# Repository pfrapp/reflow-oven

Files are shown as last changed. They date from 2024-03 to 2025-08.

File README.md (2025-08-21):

# reflow-oven
DIY reflow oven for SMD soldering

## Scope

In this project, we build an oven for reflow soldering of SMD (surface mount device)
parts, such as for instance microcontrollers etc.
In general, it will help to move away from THT (through hole technology)
boards and enter the realm of SMT (surface mount technology) boards.
This saves space, helps to get rid of evaluation-board-style setups,
and enables fully embedded circuits.
It basically makes the PCBs more professional and less tinker-ish.

This project is inspired by a reflow oven that I had at the university.
It was a predecessor of this one that you can currently buy at Beta Layout.
https://eu.beta-layout.com/estore/order_product_details.html?wg=1&p=740

Another inspiration is this instructable
https://www.instructables.com/DIY-REFLOW-OVEN/
that shows how to build a DIY oven.

The latter resource ends up with a self-contained oven, as the author wants
to be able to use it as a stand-alone tool.
It looks really professional and solid.

In this project, I just want to get the oven working in a first step.
Furthermore, I want to use the oven to build an improved version of the controller board
(kind of in a bootstrapping manner).
Also, the oven shall be usable and controllable from my computer.
For this reason, I will not disassemble the oven itself nor use an LCD
display, but just create an MVP which is a controller that
uses the actual oven as is.

## Idea

The general idea is to use an off-the-shelf pizza oven as the central
heating element or oven.
In the process of reflow soldering, we need to ensure that the temperature
follows a *reflow soldering profile*.

Therefore, we use a temperature probe to measure the temperature and
feed it back to a controller which generates the control signal.

This is a PWM signal,
as the temperature dynamics is very slow and hence acts as a natural
low-pass filter.
As the controller can only provide the signal, but not the actual power,
we use a solid-state relay (SSR) as the actuator
in order to transform the uC signal
to a mains voltage signal.

The controller algorithm runs on a Raspberry Pi. It is connected via
USB to a Cortex M4 microcontroller. The latter is used
to acquire the temperature signal and to create the PWM signal.

## Components

Here is an overview of the essential required components.

| Component | Manufacturer | Description | Distributor | Order no. | Price (Euro)  |
|---|---|---|---|---|---|
| SSR | Finder | Steck-/Printrelais, 1x UM, 250V/10A, 5V, RM3,2 | Reichelt | FIN 43.41.7 5V  | 5.95 |
| Temperatur probe | UNI-T | Temperaturfuehler, Typ K, universal | Reichelt | UT TF-K | 3.95 |
| Cortex M4 Eval Board | TI | TM4C1236 Evaluation Board with breakout pins | DigiKey | 2314937 | ca. 18 |
| Pizza oven | Severin | TO 2045 Oven, 1500 W, 100 to 230 deg C | Amazon | | 60 |
| Fuse | | Feinsicherung 5x20mm, superflink (ff), 8A | Reichelt | ESKA 520.126 | ca. 2 |
| Fuse holder | | 5 x 20 mm, 250 V, 10 A, black | Reichelt | SCH 31010045 | 1.50 |
| Temperature converter | Maxim Integrated  | MAX6675 (incl. cold junction compensation) | Voelkner | R025452 | ca. 7 |

### SSR

If there is no voltage applied at the input, then pins 11 and 12
(12 being the one close to A1 and A2) are connected.
Pins 11 and 14 are not connected.

The measured resistance between A1 and A2 is 97 Ohm for the 5V DC relay.

Hypothesis: If voltage is applied between A1 and A2 (use additional 22 Ohm resistor, transistor and impedance converter),
then pins 11 and 14 are connected.

This hypothesis is confirmed (using the lab supply):
Attaching 5 V via a 22 Ohm resistor to A1, and putting A2 on ground, makes pins 11 and 14 connected (no
resistance, connectivity test is positive).
Pins 11 and 12 are then disconnected.

### Temperature probe

When the type K thermocouple is plugged into a volt meter,
one can see 0.0 mV.
This is because both the tip as well as the cold junction
are at the same temperature.

If the tip is heated by breathing at it, the voltage rises from 0.1 mV up to 0.3 mV.
When the tip is being put into an open oven that had a nominal temperature of 225 deg C,
the voltage rises to 2.0 mV or 2.1 mV.

Looking at the table from the second reference, this means that the temperature delta
is around 50 deg C (that is, ca. 70 deg C), which seems plausible given that the oven is open
and one can easily put the hand into it.

Resources
1. https://blog.beamex.com/de/thermoelement-kaltstellenkompensation-vergleichsstelle
2. https://www.omega.de/temperature/Z/pdf/z204-205iec.pdf

### Microcontroller

We use a Cortex M4 on a Tiva evaluation board.
It can be connected to the Raspberry Pi via USB.
The Raspberry Pi is connected to the host PC via Wi-Fi.

This allows
for the complete galvanic isolation between host PC
and reflow oven controller.

## Controller PCB

The controller board is a two-stage amplifier.
The signal from the microcontroller is first amplified using a BJT.
This signal is then used to control a relay.

Yet another stage is present on the Tiva board: It turned out that the
uC pins cannot reliably drive the BJT, so I introduced an impedance converter
using an OpAmp, see the following subsection.

### Impedance converter

Due to the switching of the relay, there are some voltage spikes on the transistor,
that is, on the low voltage side of the relay.

Those spikes are less pronounced when using the lab supply and more
pronounced when using the AD/DC converter.
They are there in any case though.

For this reason, an impedance converter or buffer is needed between the
uC pin and the controller board.

So far I tested the setup using this impedance converter and a lab supply
and it works.
In oder to test it without the lab supply I need a second AC/DC converter,
as the OpAmp needs a dual rail supply.

## Controller software

### Modelling of the reflow oven dynamics

The plant is modelled by a time delay followed by two first-order lag elements.

The parameters of the plant are identified by applying a step function
onto the oven. A 30% and 50% PWM signal is used for the step height.
Also, a 100% PWM step is applyied until a temperature of 100 deg C is reached.
In that case, also the cooling down is measured.

Here are some more details for the motivation of a first-order lag.
Note that we assume that there are two in order to model the
different behavior when heating and when cooling.
```
d_theta/dt = q_zu - q_ab

q_zu = K*u
q_ab = alpha*theta

K ... Proportional zur Leistung des Ofens
theta ... Abkuehlkoeffizient

d_theta/dt = K*u - alpha*theta

d_theta/dt + alpha*theta = K*u

s*Theta + alpha*Theta = K*U

(s + alpha) * Theta = K * U

G = Theta / U = K/(s + alpha)

```

Later a more complex model is used. You can find it in the Jupyter notebook.

### Control design

A PID controller is used for temperature control.
The parameters of a PI controller have been parameterized by the Ziegler-Nichols method.
Based on that, a PID controller has been manually tuned using the experimentally
identified plant.

## Tiva pin usage and connection

| Pin on Tiva | Connected with | Description |
|---|---:|---:|
| GND | Analog Thermo amplifier GND | Ground |
| PE3 | Analog Thermo amplifier between 6.8k and 18k | ADC input |
| GND | GND of BMP280 evaluation board | Ground |
| +3.3V | VCC of BMP280 evaluation board | Supply voltage |
| PA6 | SCL of BMP280 evaluation board | I2C clock |
| PA7 | SDA of BMP280 evaluation board | I2C data |
| PB6 | Digital Thermo amplifier MISO | SPI data |
| PB5 | Digital Thermo amplifier CS | SPI CS |
| PB4 | Digital Thermo amplifier Clock | SPI clock |
| PF4 | Controller board pin 2 | Relay control |

See also the following block diagram overview.

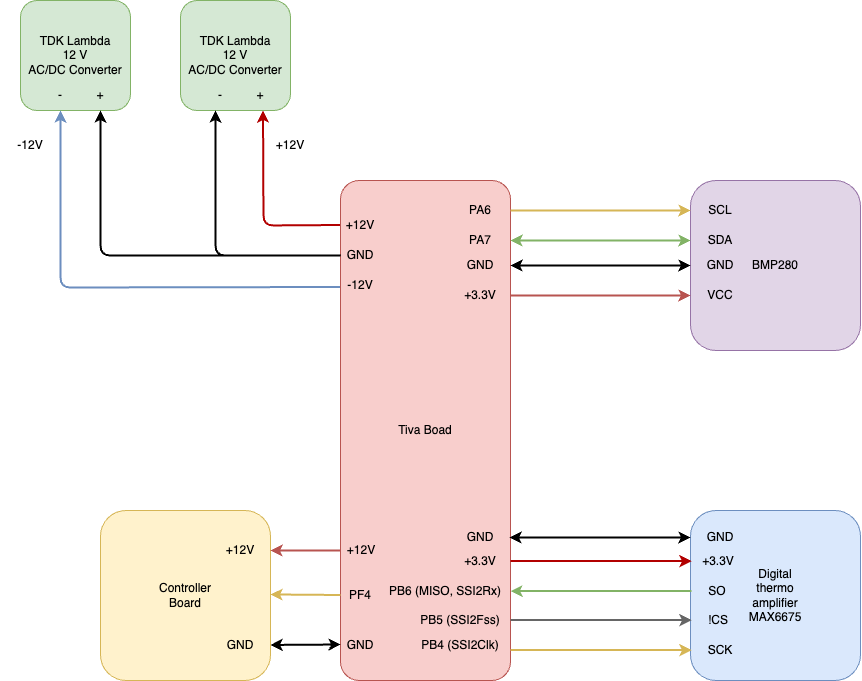
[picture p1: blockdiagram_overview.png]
Block diagram overview


## General todos

- Add note to add LED signaling open thermocouple
- Add note to add LED signaling request to open door (manually)
- Add manual with important points, for instance
  - check for polarity of diodes and LEDs
  - Alignment of ICs

## Reference solder profiles

- https://www.7pcb.com/blog/lead-free-reflow-profile
- Data sheet of my solder paste
  https://de.beta-layout.com/elektronik-shop/loetzinn-lotpaste/10753-smd-lotpaste-iso-cream/
- TI application report
  **SPRABY1A MSL Ratings and Reflow Profiles** \
  https://www.ti.com/lit/an/spraby1a/spraby1a.pdf?ts=1741440364541

## Solder reports

### First SMD soldering with this setup (Oct-30, 2024)

- Lead-free HASL PCB (that is, no ENIG)
- No uC soldered (otherwise ENIG required)
- Stencil is required
- Soldered components: 0805 C, 0805 R (contain labels), Diodes, LEDs, OpAmps and other ICs
- Some parts on the PCB did not solder well --> longer preheat time, higher peak temperature, longer reflow time
- Fragmented setup was quite a mess --> higher integration of controller boards, fixture of the BMP280
- Power via lab supply --> Use TDK Lambdas in the future
- Timing of door opening to be made easier
- Application of solder paste --> not too much, also remove where there is too much before placing the part
- Add note to check for polarity of diodes and LEDs
- Reworking requires (no clean) flux

Time above 217 deg C: 52.5 seconds (with opening the door)<br />
Time between 150 and 180 deg C: 77.0 seconds<br />
Peak temperature: 237.0 deg C

### Second SMD soldering (Dec-23, 2024)

#### Compared with the first SMD soldering, I changed the following things:
- Adjusted solder temperature profile with the goal to allow for
  - more preheat time (goal reached)
  - higher peak temperature (not reached, peak temperature was actually slightly lower)
  - longer reflow time (goal reached)
- Better solder paste application
  - I made sure to apply the solder paste in a single round. That means,
    I ensured that I had enough of the paste on the upper edge
    of the stencil.
  - Then I went down slowly *once* while pressing firmly onto the stencil.
    It is important to not go back and forth (potentially allowing for too much solder paste).
  - The described procedure favors less solder paste being applied.
    As a consequence, I did not have to remove any surplus solder paste.
- I did *not* use a separate PCB to attach the thermocouple.
  Rather than that, I braided the thermocouple wire trough the grating of the grillage.
  I made sure that the tip was directly in between two grates, thus avoiding any contact
  of the termocouple tip with the metal grates (or with a dedicated PCB).
- I made the hint to open the door more prominent so that it could be
  seen when standing at the oven and looking on to the computer screen.
- I did solder a microcontroller. It was the 64-pin TM4C123GH6PM.
  Note that I ordered lead-free HASL (that is, the ENIG finish was not necessary).

#### Observations and facts
  - When opening the door, the thermocouple was detected as open, hence
    resulting in non-usable temperature measurements.
    As this was the cool-down phase anyway, no harm was induced.
  - I slipped while placing the Cortex onto the PCB.
    Apparently that was not a show-stopper.
    As can be seen on the magnified pictures I took, the solder paste
    had not been smeared away from the Cortex, but rather only between the pins.
  - The overall solder result was surprisingly good. I did not have to do any
    reworking and hence also did not need to use the no-clean flux.
  - It was raining, but I wanted to finish before Christmas, so I used an umbrella
    to protect the oven.

#### Open todos and fixes after this second soldering round
- USB Stencil checken (also ob Anmerkungen von jlcpcb umgesetzt wurden, erst in KiCad Lib, dann im Projekt)
- Highlight beim Bestuecken (z.B. eine PDF Seite pro Teil, erstellen via KiCad Python Script)
- Sanft positionieren (z.B. Halter fuer Pinzette konstruieren?)
- Dioden Polarity dokumentieren
- LEDs Polarity dokumentieren (fuer jede einzelne LED, da potentiell unterschiedlich pro Typ und zumindest unterschiedlich markiert)
  - Bei "Tetris" artigem Bild ist das kleine Quadrat die Kathode
  - Bei Dreieck ist die Spitze die Kathode
  - Auf der Vorderseite gibt es einen kleine gruene Markierung bei der Kathode
  - Auf dem Silk ist die geschlossene Seite die Kathode, die Anode ist offen
- LED Farben fixen im Schematic (2 mehr blue, 2 weniger gruen)
- Silk fuer Montage USB (also genaue Ausrichtung)
- Cortex Stencil checken (unterschiedlich grosse Luecken auf den Seiten)
  --> hat letztlich nichts gemacht
- SMD Bauteile einsortieren
- Inventur und nachbestellen, auch Resistors, Caps.
- Art Kreuze am Stencil fuer Ausrichtung (in allen 4 Ecken)
- Thermocouple open/closed sollte beides ueber LED direkt sichtbar sein
- Reflow Oven braucht einen Baking Modus (verschiedene Dauern und Temperaturen sollten auswaehlbar sein)
- Spannungsversorgung +12V/-12V auf einen Stecker packen, damit keine unipolare Spannungsversorgung moeglich ist (die mir schon mal den uC kaputt gemacht hat)
- Widerstand oder Zener auf PF4 Signal legen
```
(GPIO Output) --- [ 4.7 kΩ Resistor ] ---+--- (OpAmp Non-Inverting Input)
                                          |
                                    [ 3.3 V Zener Diode ]
                                          |
                                         GND
```

#### Output of the Jupyter script for solder profile analysis

Time above 217 deg C: 114.99984027777778 seconds (with opening the door)<br />
Time between 150 and 180 deg C: 91.99987222222222 seconds<br />
Peak temperature: 1023.75 deg C

Note that there was an error due to the thermocouple being open.
The values are rather<br />

Time above 217 deg C: 60 seconds (with opening the door)<br />
Time between 150 and 180 deg C: 91.99987222222222 seconds<br />
Peak temperature: 233 deg C

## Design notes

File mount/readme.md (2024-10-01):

This folder contains the 3D models for the PCB and stencil mount.
Those are used to fixate the PCB and strencil while applying the soldering paste.

The idea is to be able to fixate the PCB and the stencil independently via screws.
No tape shall be used.

PCB without stencil
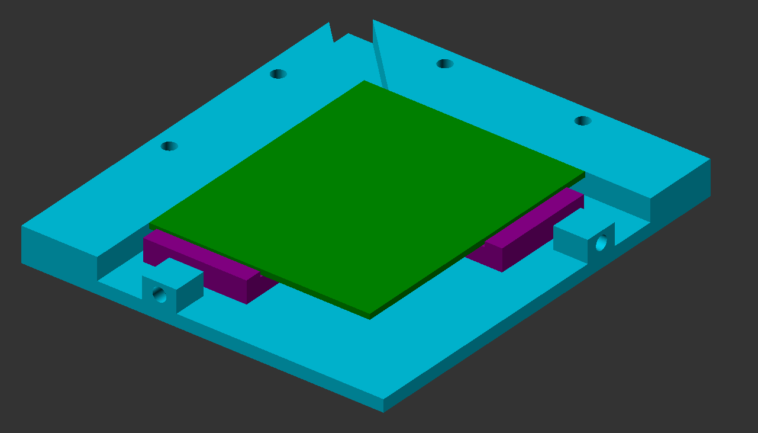
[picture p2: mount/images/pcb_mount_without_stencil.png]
PCB mount without stencil


PCB with stencil
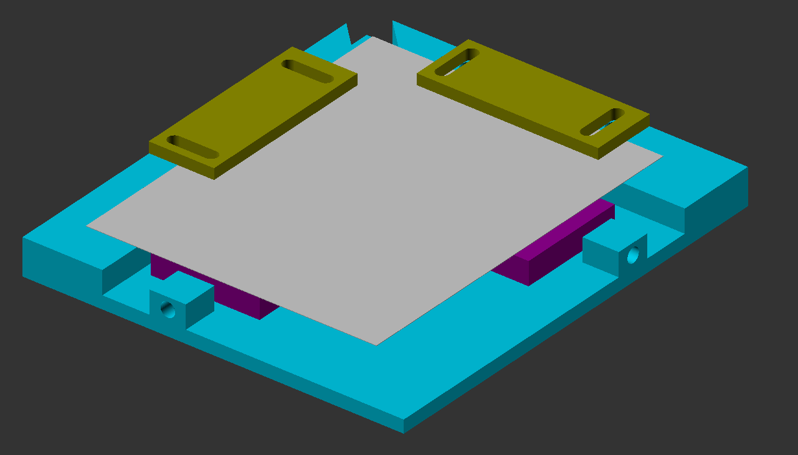
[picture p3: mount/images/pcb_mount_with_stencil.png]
PCB mount with stencil


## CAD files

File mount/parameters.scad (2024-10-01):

// Screw threads.
// Note that the depth is increased by 0.1 mm as compared
// to the data sheet.
// The diameter corresponds to the d3 from the data sheet,
// and the depth correponds to the L.

// M2
g_M2_thread_diameter = 3.2;
g_M2_thread_depth    = 4.1;

// M3
g_M3_thread_diameter = 4.0;
g_M3_thread_depth    = 5.8;

// Through holes.
// See for instance https://de.wikipedia.org/wiki/Durchgangsbohrung
g_M2_through_hole_diameter = 2.4;
g_M3_through_hole_diameter = 3.4;
g_M3_through_hole_diameter_large = 3.6;

// Offset between holes in stencil mount
stencil_mount_hole_offset = 40.0;

// Outer dimension of the PCB mount part
height_mount = 10.0;
length_mount = 105.0;
width_mount = 120.0;

// Thickness of the wall where the PCB is pushed against.
// This is used for the margins of the stencil which
// is larger than the PCB.
wall_thickness_mount = 14.0;

// Space for the stencil (at the top and left).
// Actually this is space for the stencil mount.
stencil_space = 8.0;

// Height of the PCB
height_pcb = 1.6;

// Height of the stencil
height_stencil = 0.15;

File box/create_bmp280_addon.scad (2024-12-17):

// Mount for the BMP280 temperature sensor (evaluation board).
// Should at some point be unified with the other boxes.
//
// BMP280 evaluation board
// - outer distances of holes: 13.30 mm
// - inner distances of holes: 7.20 mm
//
// --> Double hole diameter = 13.30 - 7.20 = 3.05 mm
// 2x M2 mit Unterlegscheibe (statt M3) wg. Positionstoleranz
//
// Distance between hole centeres: 0.5 * (13.30 + 7.20) = 10.25 mm
// (likely nominally 4 * 2.54 mm = 10.16 mm)
//
// Breite Auflageflaeche: 15 mm (mit Bohrungen mittig)
// Hoehe Auflageflaeche: 25 mm (Bohrungen jeweils am Rand)
//
// Hoehe des Bauteils: 20 mm


g_fn = 90;

g_spacing = 10.16;
g_holes_y = [-g_spacing / 2.0, g_spacing / 2.0];

// M2
g_M2_thread_diameter = 3.2;
g_M2_thread_depth    = 4.1;
g_M2_through_hole_diameter = 2.4;

width = 11;
height = 25;

roundness = 2;

module entity() {
    difference() {
        union() {   
            // Cube
            translate([-(width-roundness)/2,-(height-roundness)/2,10]) {
                minkowski() {
                sphere(r = 1, $fn = g_fn);
                linear_extrude(20-roundness, center=true)
                    square([width-roundness, height-roundness]);
                }
            }
            linear_extrude(3, center=false)
                scale([1.0, 2.0, 1.0])
                    circle(r = 12, $fn = g_fn);
        }
        union() {
            // Through holes
            for (y = g_holes_y) {
                translate([0.0, y, 0.0])
                    cylinder(h = 20, d = g_M2_through_hole_diameter, $fn = g_fn);
            }
            // Holes for thread mount
            for (y = g_holes_y) {
                translate([0.0, y, 20.0 - g_M2_thread_depth])
                    cylinder(h = g_M2_thread_depth, d = g_M2_thread_diameter, $fn = g_fn);
            }
        }
    }
}



entity();

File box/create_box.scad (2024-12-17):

// Box for the reflow controller
//
// Aktor/Ansteuerung Board Dimension: 90 x 60
// Bohrmuster: 82 x 52
// Rand: 10 links (hin zum uC), 20 rechts (hin zum Ofen und Netzspannung)

// Sensor/Digital Thermocouple Board Dimesion: 70 x 50
// Bohrmuster: 62 x 42
// Hinweis: Die Bohrung oben rechts ist um ca. 0.3 mm in y-Richtung verschoben.


// Notwendige Aenderungen:
// - Noch mehr Platz beim Stromanschluss vorsehen
// - Bohrungen fuer das Tiva Board mit Impedance Converter einfuegen
// - Deckel an der Seite abschliessen


g_fn = 90;

// Nominell 8 mm (gemessen), plus 0.2 mm Toleranz wg. 3D Drucker
d_stromkabel = 8.0 + 0.2;

g_bohrmuster_relay_board_x = [-41, 41];
g_bohrmuster_relay_board_y = [-26, 26];

g_bohrmuster_thermo_board_x = [-31, 31];
g_bohrmuster_thermo_board_y = [-21, 21];

module box() {
    translate([-60,-40,0])
        difference() {
            union() {
                cube([140,80,32]);
                translate([136,80,0])
                    cube([4,58,32]);
            }
            translate([0,2,1.5])
                cube([136,76,32.5]);
            translate([0,80,2])
                cube([136,115,32]);
            translate([0,0,2])
                cube([60,160,32]);
            translate([0,150,2])
                cube([140,45,35]);
            translate([42,100,0])
                cube([35,80,2]);
        }
}

module halter(pattern_x, pattern_y) {
    for (x = pattern_x) {
        for (y = pattern_y) {
            translate([x,y,0]) {
                cylinder(d=10, h=10, $fn=g_fn);
            }
        }
    }
}

module halter_hutschiene(pattern_x, pattern_y) {
    for (x = pattern_x) {
        for (y = pattern_y) {
            translate([x,y,0]) {
                cylinder(d=12, h=16, $fn=g_fn);
            }
        }
    }
}

// M3
module halter_loecher(pattern_x, pattern_y) {
    for (x = pattern_x) {
        for (y = pattern_y) {
            translate([x,y,0]) {
                translate([0,0,4.2])
                    cylinder(d=4.0, h=5.8, $fn=g_fn);
                cylinder(d=3.4, h=10, $fn=g_fn);
            }
        }
    }
}

// M4
module halter_loecher_hutschiene(pattern_x, pattern_y) {
    for (x = pattern_x) {
        for (y = pattern_y) {
            translate([x,y,0]) {
                translate([0,0,7.8])
                    cylinder(d=5.6, h=8.2, $fn=g_fn);
                cylinder(d=4.6, h=16, $fn=g_fn);
            }
        }
    }
}

module kabelfuehrung() {
    for (y = [-3,15]) {
        translate([70,y,23])
            rotate([0,90,0]) {
                cylinder(d=d_stromkabel, h=20, $fn=g_fn);
            }
    }
}

module quarter_cylinder(r, h) {
    difference() {
        cylinder(h=h, r=r, $fn=g_fn);
        translate([-r,0,0])
            cube([2*r, 2*r, 4*h], center=true);
        translate([0,-r,0])
            cube([2*r, 2*r, 4*h], center=true);
    }
}

// Bohrungen fuer die Laborstecker.
// Durchmesser: 8 mm (daher 8.2 mm wg. Toleranz).
module bohrungen_laborstecker() {
    g_laenge = 90.0;
    g_wanddicke = 5;
    g_hoehe = 30;
    
    
    d_bohrung_laborstecker = 8.2;
    translate([0,g_wanddicke,g_hoehe/2])
        rotate([90,0,0])
            linear_extrude(g_wanddicke, center=false) {
                translate([g_laenge/4,0,0])
                    circle(d=d_bohrung_laborstecker, $fn=g_fn);
                translate([g_laenge/2,0,0])
                    circle(d=d_bohrung_laborstecker, $fn=g_fn);
            }
    // Beschriftung
    font_size = 4.5;
    text_depth = 2;
    translate([g_laenge/4+0*d_bohrung_laborstecker,0,3*g_hoehe/4])
        rotate([90,0,0])
            translate([0,0,-text_depth])
                linear_extrude(text_depth, center=false)
                    text("T(-)",
                        font = "Arial Black",
                        size = font_size,
                        valign = "bottom",
                        halign = "center");
    translate([g_laenge/2+0*d_bohrung_laborstecker,0,3*g_hoehe/4])
        rotate([90,0,0])
            translate([0,0,-text_depth])
                linear_extrude(text_depth, center=false)
                    text("T(+)",
                        font = "Arial Black",
                        size = font_size,
                        valign = "bottom",
                        halign = "center");
}

module verbindung_halter() {
    // Grundform
    grundform_points = [[-52, -38], [-52, 40], [-38, 60], [-38, 150],
                        [55, 150], [38, 110], [38, 60], [42, 40], [42, -38],
                        [30, -38], [30, 40], [25, 60], [25, 110], [35, 140],
                        [-25, 140], [-25, 55], [-40, 35], [-40, -38]
                       ];
    linear_extrude(3.0)
        minkowski() {
            polygon(grundform_points);
            circle(r=2, $fn = g_fn);
        }
}

module entity() {
    difference() {
        union() {
            box();
            translate([-5,0,0])
                halter(g_bohrmuster_relay_board_x, g_bohrmuster_relay_board_y);
            translate([0,80,0])
                halter(g_bohrmuster_thermo_board_x, g_bohrmuster_thermo_board_y);
            // Hutschiene
            translate([-30,145,0])
                halter_hutschiene([0, 75], [0]);
            translate([80,40,2])
                rotate([0,0,180])
                    quarter_cylinder(r=12, h=30);
            translate([80,-40,2])
                rotate([0,0,90])
                    quarter_cylinder(r=12, h=30);
            verbindung_halter();
        }
        translate([-5,0,0])
            halter_loecher(g_bohrmuster_relay_board_x, g_bohrmuster_relay_board_y);
        translate([0,80,0])
            halter_loecher(g_bohrmuster_thermo_board_x, g_bohrmuster_thermo_board_y);
        // Loecher zur Befestigung des Deckels
        translate([80,0,23])
            halter_loecher([-5], [-35, 35]);
        // Loecher zur Befestigung der Hutschiene
        translate([-30,145,0])
            halter_loecher_hutschiene([0, 75], [0]);
        kabelfuehrung();
        translate([80,40,0])
            rotate([0,0,90])
                bohrungen_laborstecker();
    }
}


entity();
// translate([-16,0,32])
//     lid();

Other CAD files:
box/create_lid.scad
box/create_tiva_box_addon.scad
box/lid_part.scad
mount/create_assembly.scad
mount/create_pcb.scad
mount/create_pcb_mount.scad
mount/create_plate.scad
mount/create_stencil.scad
mount/create_stencil_mount.scad

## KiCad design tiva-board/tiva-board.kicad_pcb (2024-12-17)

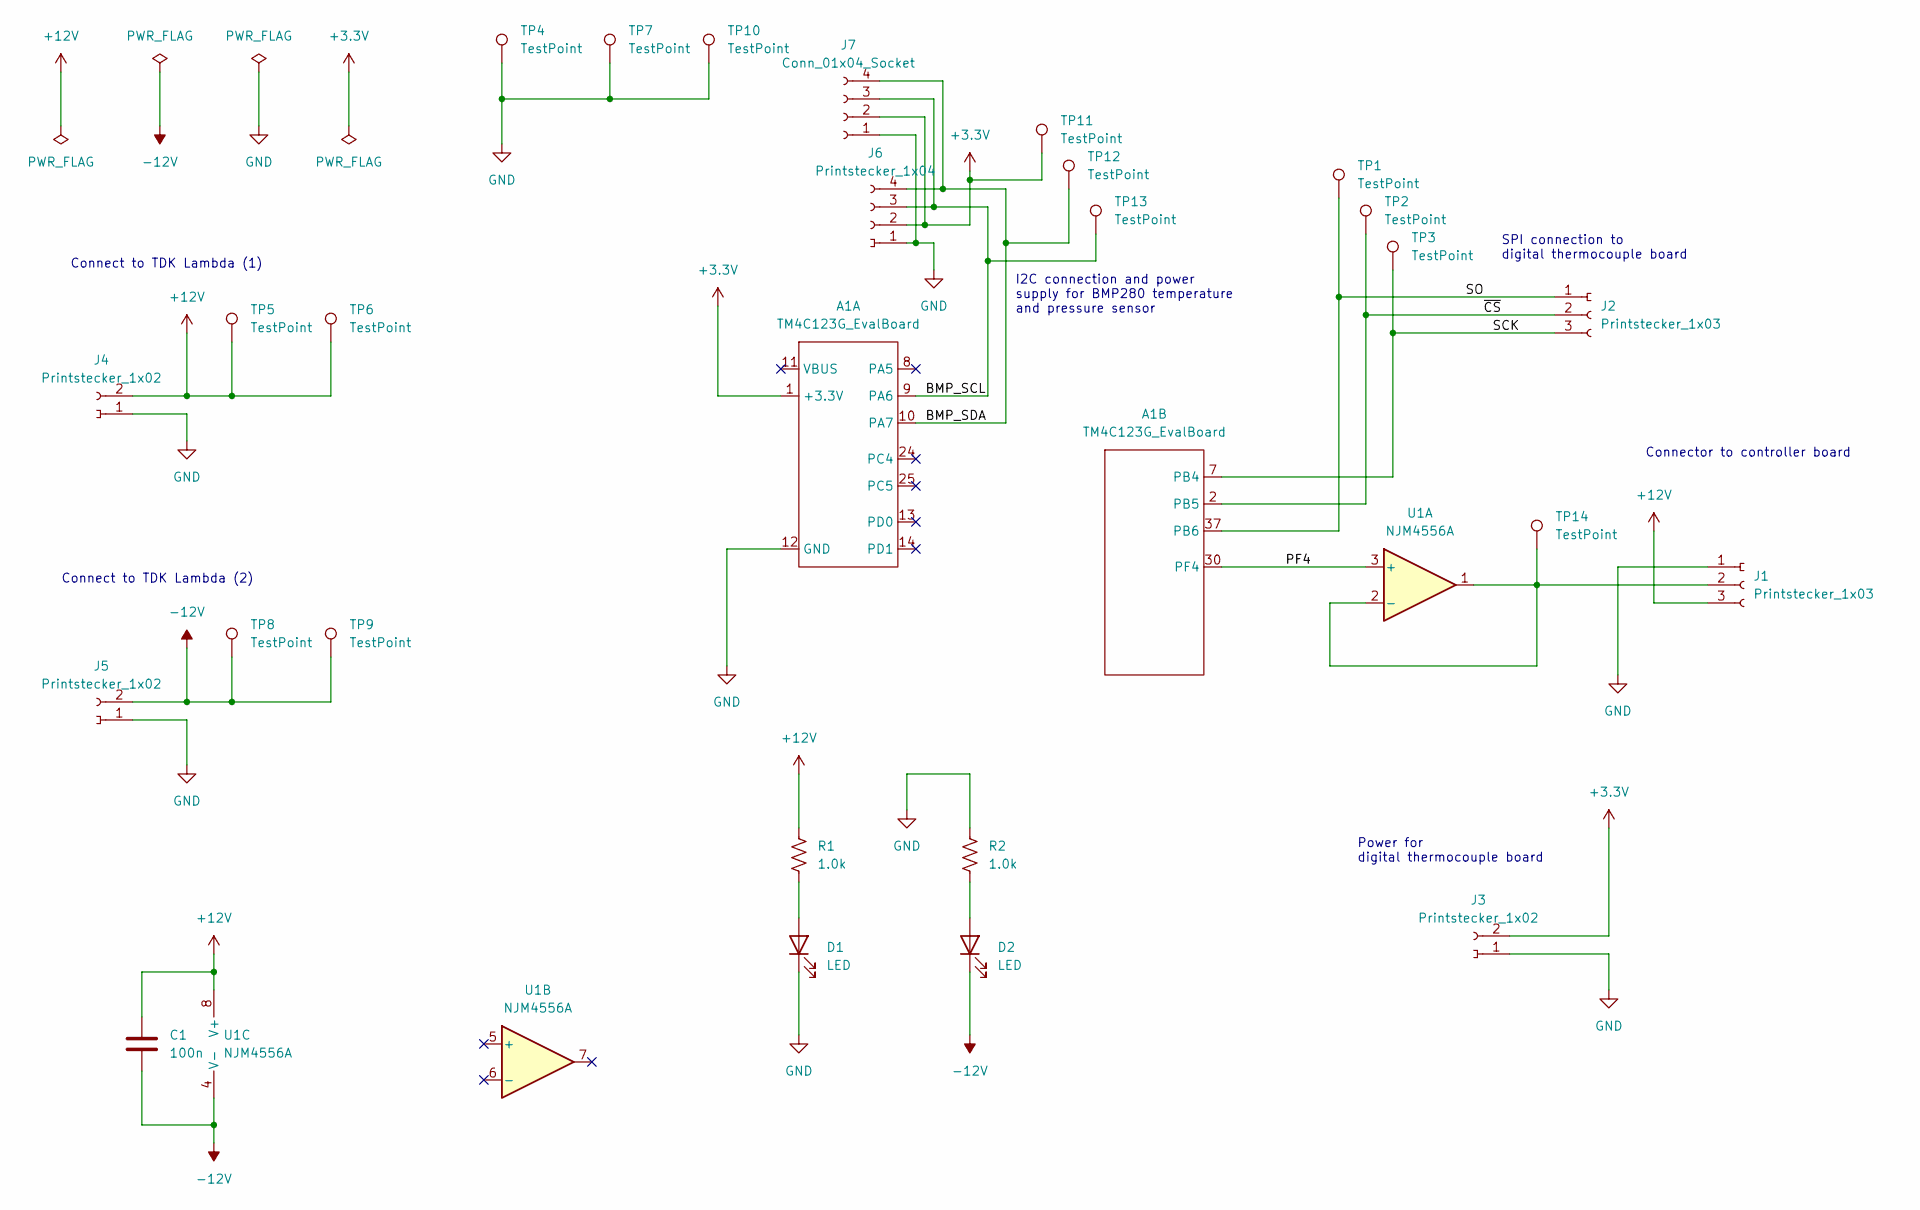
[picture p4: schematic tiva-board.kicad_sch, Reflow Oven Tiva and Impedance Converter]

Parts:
A1: TM4C123G_EvalBoard
C1: 100n; C_Disc_D5.0mm_W2.5mm_P2.50mm
D1, D2: LED; LED_D5.0mm
J1, J2: Printstecker_1x03; printstecker_1x03_P2.54mm
J3, J4, J5: Printstecker_1x02; printstecker_1x02_P2.54mm
J6: Printstecker_1x04; printstecker_1x04_P2.54mm
J7: Conn_01x04_Socket; PinSocket_1x04_P2.54mm_Vertical
R1, R2: 1.0k; R_Axial_DIN0207_L6.3mm_D2.5mm_P10.16mm_Horizontal
TP1, TP2, TP3, TP6, TP9, TP11, TP12, TP13, TP14: TestPoint; TestPoint_Pad_2.0x2.0mm
TP4, TP5, TP7, TP8, TP10: TestPoint; TestPoint_Plated_Hole_D2.0mm
U1: NJM4556A; DIP-8_W7.62mm

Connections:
+3.3V: A1.1 (+3.3V), J3.2, J6.2, J7.2, TP11.1
+12V: C1.1, J1.3, J4.2, R1.1, TP5.1, TP6.1, U1.8 (V+)
-12V: C1.2, D2.1 (K), J5.2, TP8.1, TP9.1, U1.4 (V-)
/BMP_SCL: A1.9 (PA6), J6.3, J7.3, TP13.1
/BMP_SDA: A1.10 (PA7), J6.4 (Pin_3), J7.4, TP12.1
/PF4: A1.30 (PF4), U1.3 (+)
/SCK: A1.7 (PB4), J2.3, TP3.1
/SO: A1.37 (PB6), J2.1, TP1.1
/~CS: A1.2 (PB5), J2.2, TP2.1
GND: A1.12 (GND), A1.31 (GND), D1.1 (K), J1.1, J3.1, J4.1, J5.1, J6.1, J7.1, R2.1, TP4.1, TP7.1, TP10.1
unnamed: D1.2 (A), R1.2
unnamed: D2.2 (A), R2.2
unnamed: J1.2, TP14.1, U1.1, U1.2 (-)

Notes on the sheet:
Power for digital thermocouple board
I2C connection and power supply for BMP280 temperature and pressure sensor
Connect to TDK Lambda (2)
Connect to TDK Lambda (1)
Connector to controller board
SPI connection to digital thermocouple board

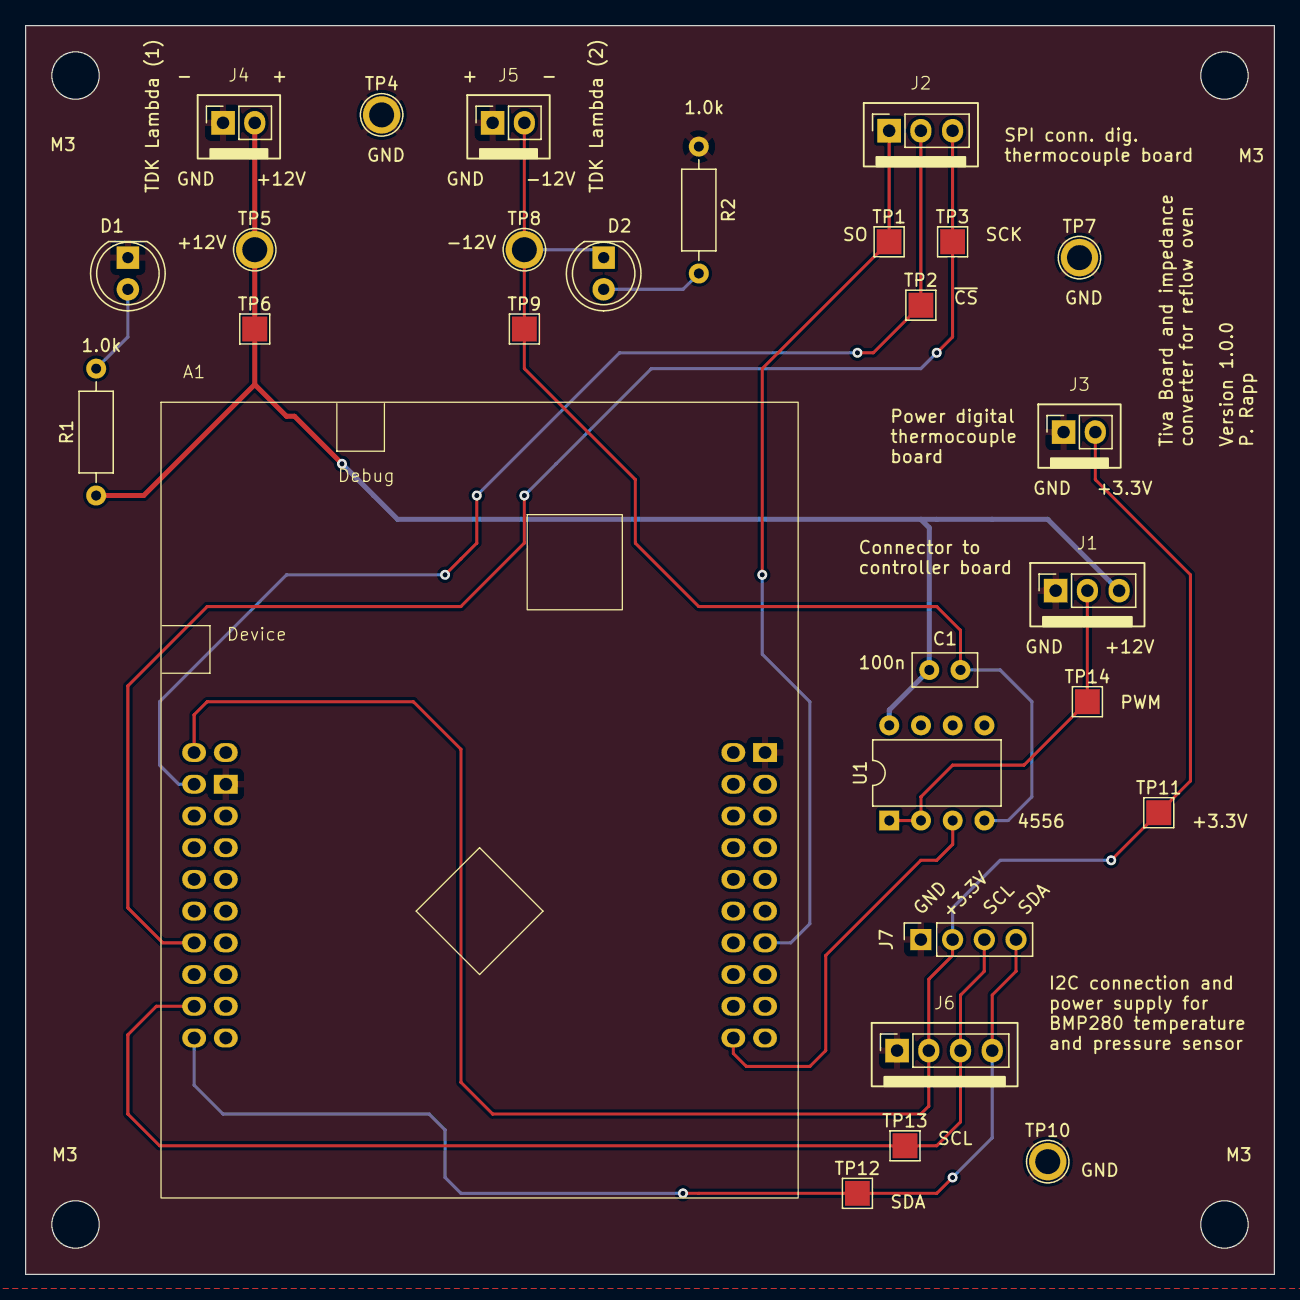
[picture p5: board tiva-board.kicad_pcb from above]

Board: 2 copper layers, 100.0 x 100.0 mm, 28 parts (0 on the bottom side), 13 nets.

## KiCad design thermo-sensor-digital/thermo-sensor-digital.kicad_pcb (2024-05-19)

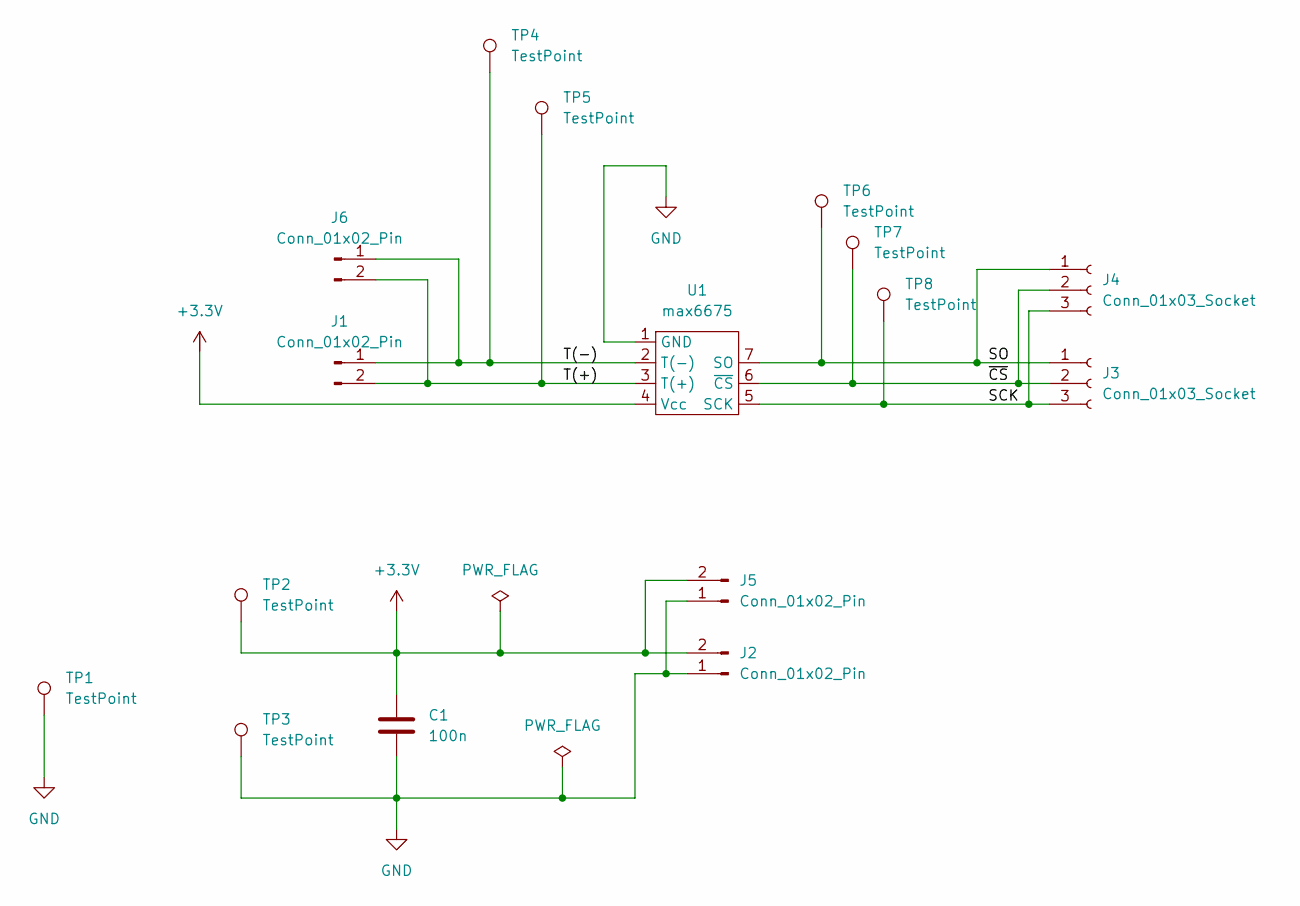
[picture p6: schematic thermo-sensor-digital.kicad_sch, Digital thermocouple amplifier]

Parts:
C1: 100n; C_Disc_D5.0mm_W2.5mm_P2.50mm
J1, J2, J5, J6: Conn_01x02_Pin; PinSocket_1x02_P2.54mm_Vertical
J3, J4: Conn_01x03_Socket; PinSocket_1x03_P2.54mm_Vertical
TP1: TestPoint; TestPoint_THTPad_4.0x4.0mm_Drill2.0mm
TP2, TP4, TP5, TP6, TP7, TP8: TestPoint; TestPoint_Pad_2.0x2.0mm
TP3: TestPoint; TestPoint_Plated_Hole_D2.0mm
U1: max6675

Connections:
+3.3V: C1.1, J2.2, J5.2, TP2.1, U1.4 (Vcc)
/SCK: J3.3, J4.3, TP8.1, U1.5 (SCK)
/SO: J3.1, J4.1, TP6.1, U1.7 (SO)
/T(+): J1.2, J6.2, TP5.1, U1.3 (T(+))
/T(-): J1.1, J6.1, TP4.1, U1.2 (T(-))
/~CS: J3.2, J4.2, TP7.1, U1.6 (~CS)
GND: C1.2, J2.1, J5.1, TP1.1, TP3.1, U1.1 (GND)

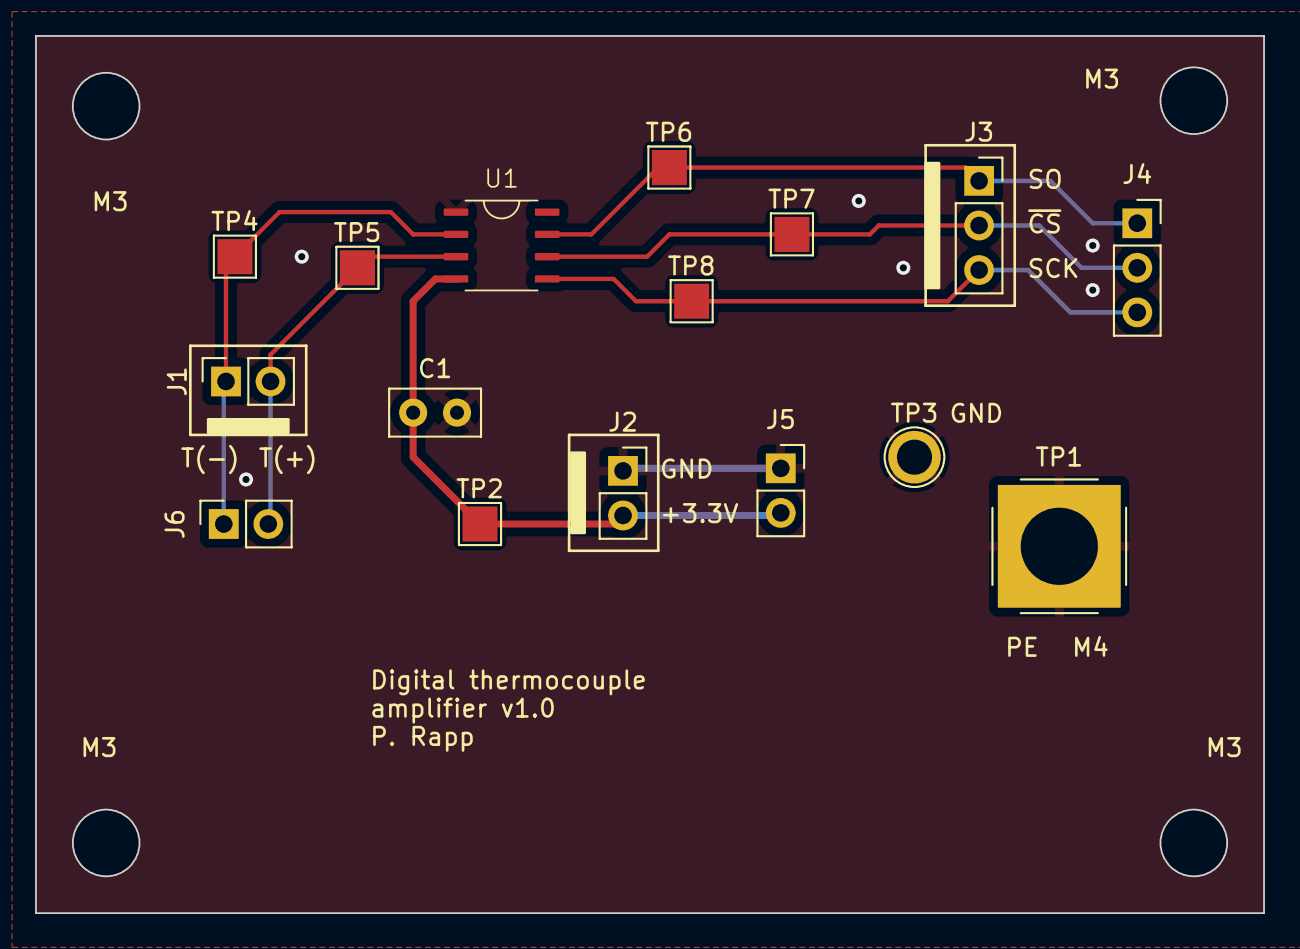
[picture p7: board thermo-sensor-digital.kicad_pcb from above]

Board: 2 copper layers, 70.0 x 50.0 mm, 16 parts (0 on the bottom side), 7 nets.

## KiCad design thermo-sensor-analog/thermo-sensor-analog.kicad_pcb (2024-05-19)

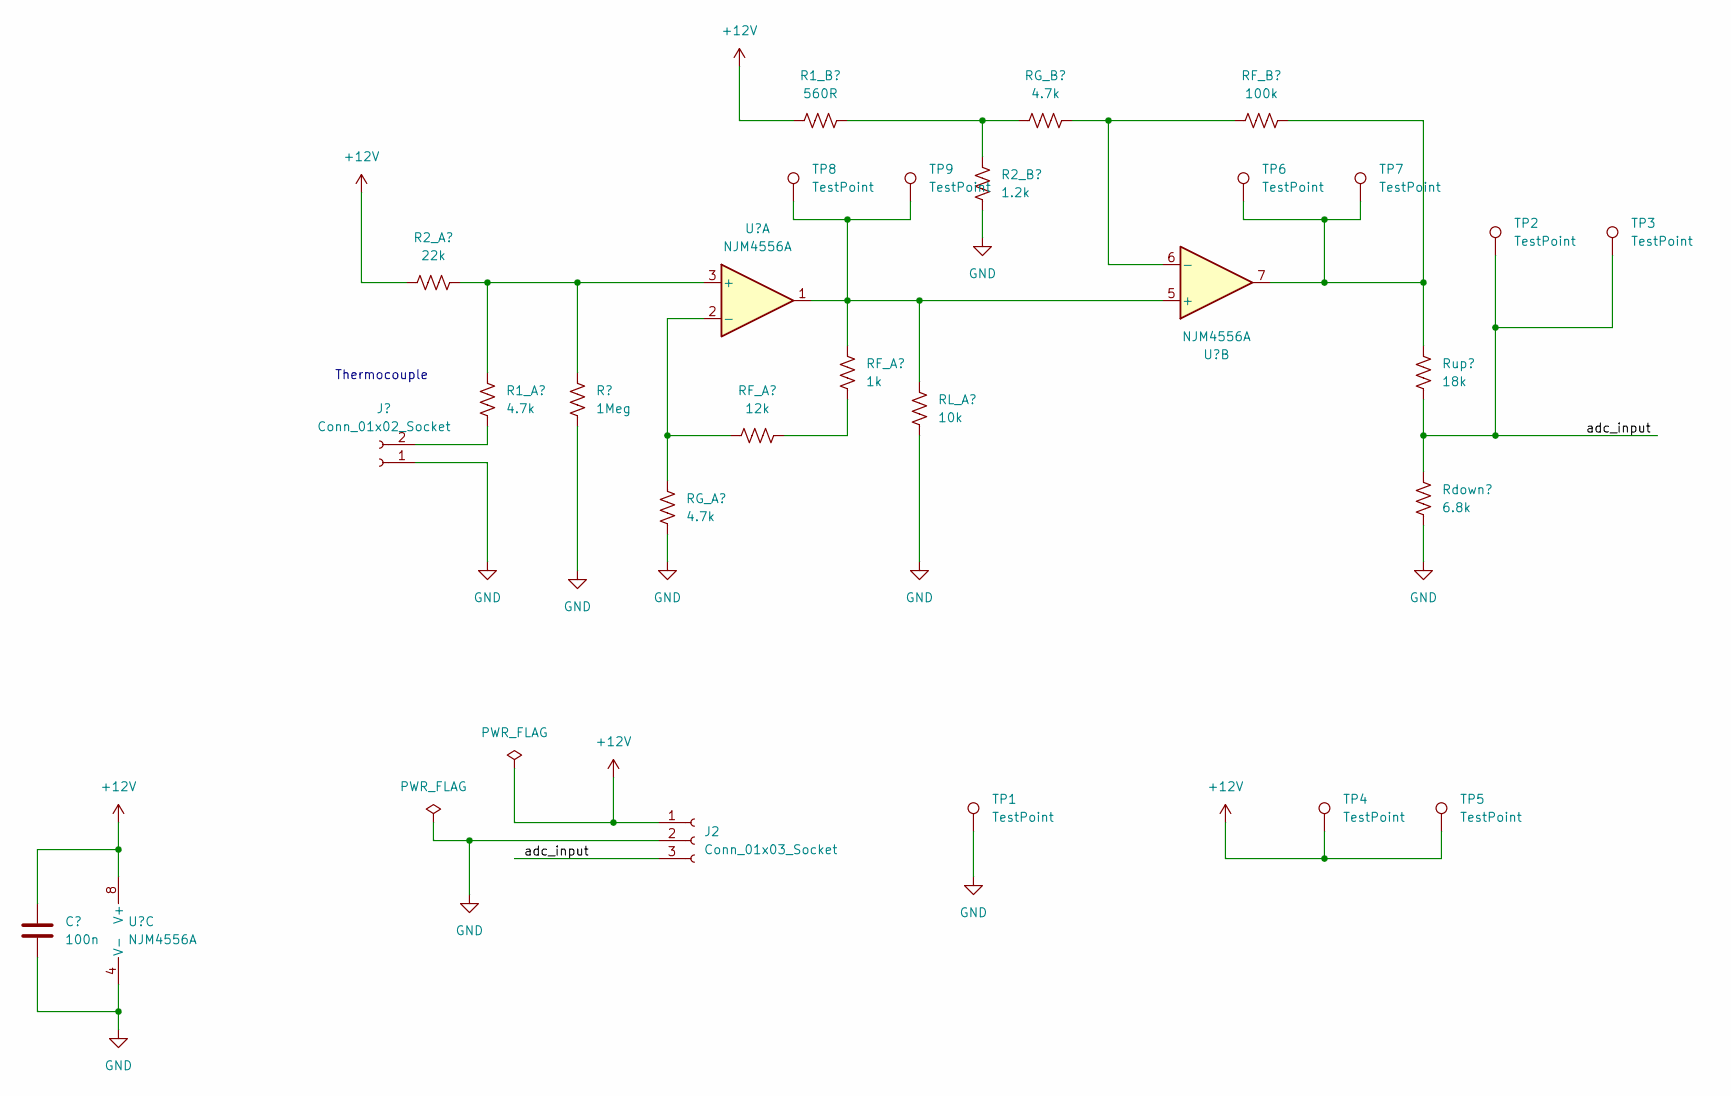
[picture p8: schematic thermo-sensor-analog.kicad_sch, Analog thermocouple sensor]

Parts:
C1: 100n; C_Disc_D5.0mm_W2.5mm_P2.50mm
J1: Conn_01x02_Socket; PinSocket_1x02_P2.54mm_Vertical
J2: Conn_01x03_Socket; PinSocket_1x03_P2.54mm_Vertical
R1: 22k; R_Axial_DIN0207_L6.3mm_D2.5mm_P10.16mm_Horizontal
R2, R4, R10: 4.7k; R_Axial_DIN0207_L6.3mm_D2.5mm_P10.16mm_Horizontal
R3: 1Meg; R_Axial_DIN0207_L6.3mm_D2.5mm_P10.16mm_Horizontal
R5: 12k; R_Axial_DIN0207_L6.3mm_D2.5mm_P10.16mm_Horizontal
R6: 560R; R_Axial_DIN0207_L6.3mm_D2.5mm_P10.16mm_Horizontal
R7: 1k; R_Axial_DIN0207_L6.3mm_D2.5mm_P10.16mm_Horizontal
R8: 10k; R_Axial_DIN0207_L6.3mm_D2.5mm_P10.16mm_Horizontal
R9: 1.2k; R_Axial_DIN0207_L6.3mm_D2.5mm_P10.16mm_Horizontal
R11: 100k; R_Axial_DIN0207_L6.3mm_D2.5mm_P10.16mm_Horizontal
R12: 18k; R_Axial_DIN0207_L6.3mm_D2.5mm_P10.16mm_Horizontal
R13: 6.8k; R_Axial_DIN0207_L6.3mm_D2.5mm_P10.16mm_Horizontal
TP1, TP2, TP4, TP6, TP8: TestPoint; TestPoint_Plated_Hole_D2.0mm
TP3, TP5, TP7, TP9: TestPoint; TestPoint_Pad_2.0x2.0mm
U1: NJM4556A; DIP-8_W7.62mm

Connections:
+12V: C1.1, J2.1, R1.1, R6.1, TP4.1, TP5.1, U1.8 (V+)
/adc_input: J2.3, R12.1, R13.2, TP2.1, TP3.1
GND: C1.2, J1.1, J2.2, R3.1, R4.1, R8.1, R9.1, R13.1, TP1.1, U1.4 (V-)
unnamed: J1.2, R2.1
unnamed: R5.2, R7.1
unnamed: R6.2, R9.2, R10.1
unnamed: R11.2, R12.2, TP6.1, TP7.1, U1.7
unnamed: R1.2, R2.2, R3.2, U1.3 (+)
unnamed: R4.2, R5.1, U1.2 (-)
unnamed: R7.2, R8.2, TP8.1, TP9.1, U1.1, U1.5 (+)
unnamed: R10.2, R11.1, U1.6 (-)

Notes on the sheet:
Thermocouple

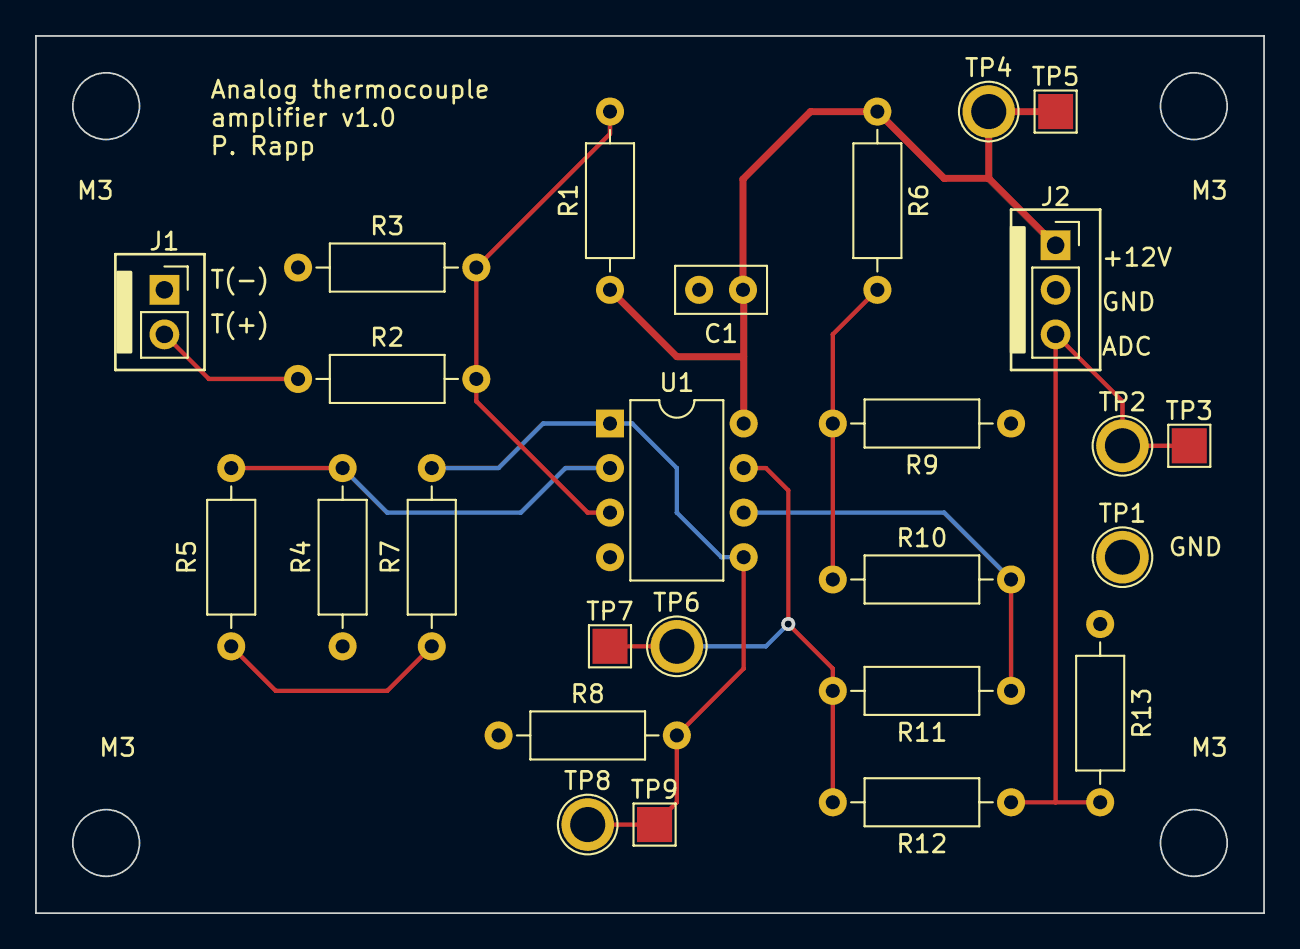
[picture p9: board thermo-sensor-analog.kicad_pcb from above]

Board: 2 copper layers, 70.0 x 50.0 mm, 26 parts (0 on the bottom side), 11 nets.

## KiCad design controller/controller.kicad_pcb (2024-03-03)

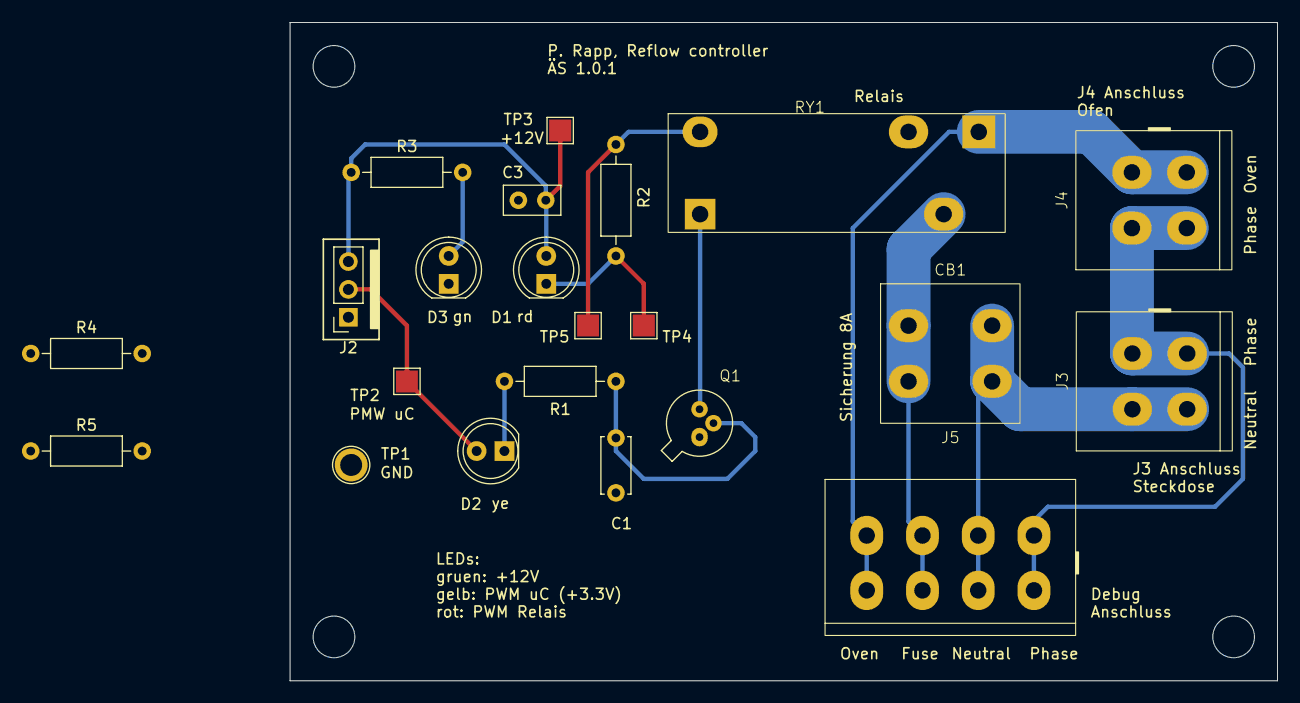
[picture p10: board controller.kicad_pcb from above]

Board: 2 copper layers, 90.0 x 60.0 mm, 22 parts (0 on the bottom side), 14 nets.

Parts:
C1: 1n; C_Disc_D5.0mm_W2.5mm_P5.00mm
C3: 100n; C_Disc_D5.0mm_W2.5mm_P2.50mm
CB1: FPG4
D1: LED rd; LED_D5.0mm
D2: LED ye; LED_D5.0mm
D3: LED gn; LED_D5.0mm
J2: Conn_01x03_Socket; PinSocket_1x03_P2.54mm_Vertical
J3, J4: WAGO 236-402
J5: WAGO 236-404
Q1: 2N2222
R1: 100R; R_Axial_DIN0207_L6.3mm_D2.5mm_P10.16mm_Horizontal
R2: 150R; R_Axial_DIN0207_L6.3mm_D2.5mm_P10.16mm_Horizontal
R3: 3.9k; R_Axial_DIN0207_L6.3mm_D2.5mm_P10.16mm_Horizontal
R4, R5: 47R; R_Axial_DIN0207_L6.3mm_D2.5mm_P10.16mm_Horizontal
RY1: FIN_43.41.7; FIN 43.41.7
TP1: TestPoint; TestPoint_Plated_Hole_D2.0mm
TP2, TP3, TP4, TP5: TestPoint; TestPoint_Pad_2.0x2.0mm

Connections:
+12V: C3.1, D1.2 (A), J2.3, R3.1, R4.1, TP3.1
/Fuse: CB1.1 (A), CB1.2 (B), J5.3 (C), J5.4 (D), RY1.3 (11)
/Oven: J4.3 (C), J4.4 (D), J5.1 (A), J5.2 (B), RY1.5 (14)
AC: J3.3 (C), J3.4 (D), J4.1 (A), J4.2 (B), J5.7 (G), J5.8 (H)
Earth: CB1.3 (C), CB1.4 (D), J3.1 (A), J3.2 (B), J5.5 (E), J5.6 (F)
GND: C1.2, C3.2, D3.1 (K), J2.1, Q1.1 (E), TP1.1
unnamed: D1.1 (K), R2.1, R5.2, TP4.1
unnamed: D2.2 (A), J2.2, TP2.1
unnamed: D2.1 (K), R1.1
unnamed: D3.2 (A), R3.2
unnamed: C1.1, Q1.2 (B), R1.2
unnamed: Q1.3 (C), RY1.2 (A2)
unnamed: R4.2, R5.1
unnamed: R2.2, RY1.1 (A1), TP5.1

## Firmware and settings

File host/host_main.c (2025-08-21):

//
// P. Rapp, Mar-23, 2024
// Copied over from the self-balancing robot host main file.
//
// This is the main host program that runs the controller for
// the reflow oven.
//
// We try and start with a PI controller.
//
// This program is also used for the system identification
// by disabling the controller and giving a step function
// onto the system (that is, the oven).
//

// C library headers
#include <stdio.h>
#include <stdlib.h>
#include <string.h> // for memset

// Linux headers
#include <fcntl.h>   // Contains file controls like O_RDWR
#include <errno.h>   // Error integer and strerror() function
#include <termios.h> // Contains POSIX terminal control definitions
#include <unistd.h>  // write(), read(), close()
#include <math.h>
#include <sys/utsname.h> // For determining on which OS we are running

#include "usb_serial_data.h"
#include "logging.h"
#include "timing.h"
#include "usb_serial.h"
#include "bmp.h"
#include "signals.h"
#include "solder_profile.h"

// Currently supported platforms
enum {
    platform_mac = 0,    // macOS
    platform_rpi = 1,     // Raspberry Pi running Raspian
    platform_invalid = 2
};

// Current mode
enum
{
    operation_mode_turn_off = 0,             // Just turn the PWM off.

    operation_mode_system_identification,    // Excert a step function for system identification.

    operation_mode_control,                  // Run the controller to follow
                                             // the reflow temperature profile.

    operation_mode_test,                     // Short solder run: follow a 5 second profile
                                             // which should not actually
                                             // heat up the ofen that much.

    operation_mode_invalid                   // Invalid operation mode.
};

int get_platform() {
    struct utsname unameData;
    uname(&unameData);
    if (strcmp(unameData.sysname, "Darwin") == 0) {
        return platform_mac;
    } else if (strcmp(unameData.sysname, "Linux") == 0) {
        return platform_rpi;
    }

    printf("uname sysname: %s\n", unameData.sysname);
    return platform_invalid;
}


enum {
    // Open-loop control, use the control signal from the file.
    open_loop = 0,
    // Closed-loop control, use the reference signal from the file.
    closed_loop
};

int main(int argc, char *argv[])
{

    // Determine the OS (macOS or Raspian).
    int platform = get_platform();
    if (platform == platform_invalid) {
        printf("Could not determine your OS, exiting\n");
        return -1;
    }

    //
    // On macOS, you can find the name of the virtual COM port by issuing
    // $ system_profiler SPUSBDataType
    // on the terminal.
    // Then you find the serial number of the respective USB device,
    // for which you can grep in /dev
    // $ cd /dev
    // $ ll | grep -ie 'the_serial_number'
    //
    // Note that the In-Circuit Debug Interface has
    // Serial Number: 0E230906
    // cu.usbmodem0E2309061
    //
    // On the Raspberry Pi, the name of the virtual COM
    // port is /dev/ttyACM0
    //
    // Regarding the Tiva:
    // For communicating (instead of flashing and debugging), you want to use the actual USB device.
    // (Change the switch on the board from Debug to Device).
    //
    const char virtualCOMPortNameRaspberryPi[] = "/dev/ttyACM0";
    const char virtualCOMPortNameMac[] = "/dev/cu.usbmodem123456781";
    const char *virtualCOMPortName = NULL;
    switch(platform) {
        case platform_mac:
            virtualCOMPortName = virtualCOMPortNameMac;
            printf("* OS identified as Mac\n");
            break;
        case platform_rpi:
            virtualCOMPortName = virtualCOMPortNameRaspberryPi;
            printf("* OS identified as RPi\n");
            break;
    }

    // The USB data packet that we are sending.
    usb_serial_data_pc_to_tiva usb_packet_to_tiva;

    // The USB data packet that we are receiving from the Tiva.
    usb_serial_data_tiva_to_pc usb_packet_from_tiva;

    int err;

    int dummy1, dummy2;
    int num_values_read;

    // Time keeping
    time_keeping timing;

    // Control (and measurement) parameters.
    control_parameters control_and_measurement_parameters;

    // Measurement logging.
    measurement_logging logging;

    // BMP structures
    struct bmp2_dev bmp_device;
    struct bmp2_uncomp_data raw_bmp_data;
    struct bmp2_data physical_bmp_data;

    // Keep track of the signals associated with the reflow oven.
    reflow_oven_signals current_reflow_oven_signals;

    // Controller data
    controller ctrl;
    ctrl.pwm_controller_percent                     = 0.0;
    ctrl.reference_deg_C                            = 0.0;
    ctrl.temperature_deg_C                          = 0.0;
    ctrl.control_error_deg_C                        = 0.0;
    ctrl.integrated_control_error_deg_C_sec         = 0.0;
    ctrl.previous_control_error_deg_C               = 0.0;
    ctrl.differentiated_control_error_deg_C_per_sec = 0.0;
    ctrl.max_runtime_seconds                        = 720;
    ctrl.kP                                         = 3.0;
    ctrl.kI                                         = 0.0200;
    ctrl.kD                                         = 20.0;

    // System identification data structure.
    system_identification sys_ident;

    // Operation mode (defaults to invalid)
    int operation_mode = operation_mode_invalid;

    //
    // Set up some parameters.
    //
    sys_ident.start_time_seconds = 10.0; // 30
    sys_ident.heating_until_deg_C = 25.0; // 100
    sys_ident.max_runtime_seconds = 720; // 720
    sys_ident.maximum_heating_temperature_ever_exceeded = 0;

    // Sample time of 500 ms, corresponding to 2 Hz.
    control_and_measurement_parameters.sample_time_ms = 500;
    // Start with -1 in order to allow sample index 0 to already have captured all
    // the measurement data.
    // This is necessary because we only receive the first measurement after we
    // sent the first control signal.
    // It will still start at time 0 as we are using the sample index
    // for active waiting.
    control_and_measurement_parameters.sample_index = -1;

    control_and_measurement_parameters.request_to_turn_off = 0;

    // Retrieve the desired operation mode.
    if (argc > 1) {
        if (strcmp(argv[1], "off") == 0) {
            control_and_measurement_parameters.request_to_turn_off = 1;
            operation_mode                                         = operation_mode_turn_off;
        } else if (strcmp(argv[1], "sysident") == 0) {
            operation_mode = operation_mode_system_identification;
        } else if (strcmp(argv[1], "solder") == 0) {
            operation_mode = operation_mode_control;
        } else if (strcmp(argv[1], "test") == 0) {
            operation_mode = operation_mode_test;
        }
    }
    if (operation_mode == operation_mode_invalid) {
        printf("## No or invalid operation mode provided as first argument.\n"
               "## Valid operation modes are: off, sysident, solder, and test.\n"
               "## Exiting (with return code -1).\n");
        return -1;
    }

    // Set the runtime of the program.
    switch (operation_mode) {
        case operation_mode_turn_off:
            control_and_measurement_parameters.max_runtime_seconds = 1;
            break;

        case operation_mode_system_identification:
            control_and_measurement_parameters.max_runtime_seconds = sys_ident.max_runtime_seconds;
            break;

        case operation_mode_control:
            control_and_measurement_parameters.max_runtime_seconds = ctrl.max_runtime_seconds;
            break;

        case operation_mode_test:
            control_and_measurement_parameters.max_runtime_seconds = 5;
            break;
    }

    // Init logging and log some general parameters
    if (!control_and_measurement_parameters.request_to_turn_off) {
        logging.log_fid = fopen("signals.log", "w");
        logging.first_log_call = 1;

        // Log some parameters before the actual tabular data begins.
        // Needs to be skipped when reading the csv file.
        fprintf(logging.log_fid, "Sample time (ms): %i\n", control_and_measurement_parameters.sample_time_ms);
        fprintf(logging.log_fid, "Maximum runtime (s): %i\n", control_and_measurement_parameters.max_runtime_seconds);
    }

    printf("*\n");
    printf("* Connecting to the Tiva device via the virtual COM port.\n");
    printf("* COM port name: %s\n", virtualCOMPortName);
    printf("*\n");

    int serial_port = open(virtualCOMPortName, O_RDWR);
    if (serial_port < 0)
    {
        fprintf(stderr, "### Error %i from open()\n", errno);
        fprintf(stderr, "### Make sure the device is plugged in and the switch\n");
        fprintf(stderr, "### is set to DEVICE (not DEBUG)\n");
        fprintf(stderr, "### Exiting!\n");

         // Gave error code 13 on the Raspberry Pi
         // except when being run as root via sudo ./tiva_usb_connect
         // In order to not resort to running the program as root, add the current user
         // to the group dialout.
         // Check if the device is attached to the group dialout either via ll in the
         // /dev folder, or via stat /dev/ttyACM0 and look for Gid.
         fprintf(stderr, "### On Linux, if the error code is 13, add your user to the dialout group.\n");
         fprintf(stderr, "sudo usermod -a -G dialout $USER\n");
         fprintf(stderr, "Reboot after you did this.\n");

        return -1;
    }
    printf("Successfully opened the serial port.\n");

    //--------------------------------------------------

    // Create new termios struct, we call it 'tty' for convention
    struct termios tty;
    // Configure the tty, return on error.
    err = configure_tty(serial_port, &tty);
    if (err != 0) {
        return 1;
    }

    // Capture the time of the start of the actual program logic.
    timing.milliseconds_since_epoch_at_start = getMilliSecondsSinceEpoch();

    while (1)
    {
        float time_sec;
        float thermocouple_voltage;
        uint16_t digital_thermocouple;


        // Idle (wait) until the sampling interval is over.
        // Perhaps a callback function is more appropriate in the long term.
        do {
            timing.current_milliseconds_since_epoch = getMilliSecondsSinceEpoch();
            timing.diff_ms = timing.current_milliseconds_since_epoch - timing.milliseconds_since_epoch_at_start;
        } while (timing.diff_ms < control_and_measurement_parameters.sample_index * control_and_measurement_parameters.sample_time_ms);



        // printf("Power mode: 0x%02X\n", usb_packet_from_tiva.power_mode);
        // printf("Temperature: 0x%02X,0x%02X,0x%02X\n",
        //     usb_packet_from_tiva.temp_msb,
        //     usb_packet_from_tiva.temp_lsb,
        //     usb_packet_from_tiva.temp_xlsb);

        bmp_device.calib_param.dig_t1 = usb_packet_from_tiva.dig_T1;
        bmp_device.calib_param.dig_t2 = usb_packet_from_tiva.dig_T2;
        bmp_device.calib_param.dig_t3 = usb_packet_from_tiva.dig_T3;

        bmp_device.calib_param.dig_p1 = usb_packet_from_tiva.dig_P1;
        bmp_device.calib_param.dig_p2 = usb_packet_from_tiva.dig_P2;
        bmp_device.calib_param.dig_p3 = usb_packet_from_tiva.dig_P3;
        bmp_device.calib_param.dig_p4 = usb_packet_from_tiva.dig_P4;
        bmp_device.calib_param.dig_p5 = usb_packet_from_tiva.dig_P5;
        bmp_device.calib_param.dig_p6 = usb_packet_from_tiva.dig_P6;
        bmp_device.calib_param.dig_p7 = usb_packet_from_tiva.dig_P7;
        bmp_device.calib_param.dig_p8 = usb_packet_from_tiva.dig_P8;
        bmp_device.calib_param.dig_p9 = usb_packet_from_tiva.dig_P9;
        bmp_device.calib_param.dig_p10 = 0; // seems to not be used anyway

        raw_bmp_data.temperature = ((usb_packet_from_tiva.temp_xlsb & 0xF0) >> 4)
                                   | (usb_packet_from_tiva.temp_lsb << 4)
                                   | (usb_packet_from_tiva.temp_msb << (8+4));
        raw_bmp_data.pressure = ((usb_packet_from_tiva.press_xlsb & 0xF0) >> 4)
                                   | (usb_packet_from_tiva.press_lsb << 4)
                                   | (usb_packet_from_tiva.press_msb << (8+4));

        // printf("Trimming values:\n");
        // printf("dig_T1 = %u\n", bmp_device.calib_param.dig_t1);
        // printf("dig_T2 = %i\n", bmp_device.calib_param.dig_t2);
        // printf("dig_T3 = %i\n", bmp_device.calib_param.dig_t3);
        // printf("dig_P1 = %u\n", bmp_device.calib_param.dig_p1);
        // printf("dig_P2 = %i\n", bmp_device.calib_param.dig_p2);
        // printf("dig_P3 = %i\n", bmp_device.calib_param.dig_p3);
        // printf("----------\n");
        // printf("Temperature: 0x%08X (%u)\n", raw_bmp_data.temperature, raw_bmp_data.temperature);
        // printf("Pressure: 0x%08X (%u)\n", raw_bmp_data.pressure, raw_bmp_data.pressure);

        bmp2_compensate_data(&raw_bmp_data, &physical_bmp_data, &bmp_device);

        // Convert thermocouple voltage
        thermocouple_voltage = ((float)usb_packet_from_tiva.amp_thermocouple_voltage / 4096) * 3.3;

        // Digital thermocouple value
        digital_thermocouple = usb_packet_from_tiva.digital_amp_thermocouple & 0x0000FFFF;
        current_reflow_oven_signals.thermocouple_is_open = digital_thermocouple & 0x0004;
        if (current_reflow_oven_signals.thermocouple_is_open) {
            printf("Digital thermocouple is open\n");
            // printf("You will not receive any measurements -- Exiting!\n");
            // return -1;
        } else {
            // printf("Digital thermocouple is closed\n");
        }
        ctrl.temperature_deg_C = (digital_thermocouple >> 3) * 0.25f;
        current_reflow_oven_signals.oven_temperature_deg_C = (digital_thermocouple >> 3) * 0.25f;

        // Check if we ever exceeded the defined temperature.
        if (current_reflow_oven_signals.oven_temperature_deg_C > sys_ident.heating_until_deg_C) {
            sys_ident.maximum_heating_temperature_ever_exceeded = 1;
        }

        // Fill sample index and ambient temperature values into the current measurement sample.
        current_reflow_oven_signals.index = control_and_measurement_parameters.sample_index;
        current_reflow_oven_signals.ambient_temperature_deg_C = physical_bmp_data.temperature;

        timing.current_milliseconds_since_epoch = getMilliSecondsSinceEpoch();
        timing.diff_ms = timing.current_milliseconds_since_epoch - timing.milliseconds_since_epoch_at_start;

        //
        // Compute the control signal
        //

        switch(operation_mode) {
            case operation_mode_turn_off:
                if (control_and_measurement_parameters.request_to_turn_off) {
                    current_reflow_oven_signals.pwm_controller_percent = 0.0;
                }
                break;

            case operation_mode_system_identification:
                if (timing.diff_ms / 1000.0 < sys_ident.start_time_seconds) {
                    current_reflow_oven_signals.pwm_controller_percent = 0.0;
                } else {
                    current_reflow_oven_signals.pwm_controller_percent = 100.0;
                }
                // Disable controller if the temperature was above the defined limit.
                if (sys_ident.maximum_heating_temperature_ever_exceeded) {
                    current_reflow_oven_signals.pwm_controller_percent = 0.0;
                }
                break;

            case operation_mode_control:
            case operation_mode_test:
                // controller update function
                // controller output function
                ctrl.reference_deg_C = 0.0;
                if (current_reflow_oven_signals.index >= 0) {
                    // Take over the value from the precomputed arrays.
                    if (operation_mode == operation_mode_control) {
                        ctrl.reference_deg_C = g_solder_profile[current_reflow_oven_signals.index];
                    } else if (operation_mode == operation_mode_test) {
                        ctrl.reference_deg_C =
                            g_solder_test_profile[current_reflow_oven_signals.index];
                    }
                }
                ctrl.control_error_deg_C = ctrl.reference_deg_C - current_reflow_oven_signals.oven_temperature_deg_C;
                ctrl.integrated_control_error_deg_C_sec +=
                        control_and_measurement_parameters.sample_time_ms * 1.0e-3 * ctrl.control_error_deg_C;
                ctrl.differentiated_control_error_deg_C_per_sec =
                    (ctrl.control_error_deg_C - ctrl.previous_control_error_deg_C) /
                        (control_and_measurement_parameters.sample_time_ms * 1.0e-3);
                ctrl.pwm_controller_percent = 
                        ctrl.kP * ctrl.control_error_deg_C
                        + ctrl.kI * ctrl.integrated_control_error_deg_C_sec
                        + ctrl.kD * ctrl.differentiated_control_error_deg_C_per_sec;
                ctrl.previous_control_error_deg_C = ctrl.control_error_deg_C;

                // Limit values
                if (ctrl.pwm_controller_percent < 0.0) {
                    ctrl.pwm_controller_percent = 0.0;
                }
                if (ctrl.pwm_controller_percent > 100.0) {
                    ctrl.pwm_controller_percent = 100.0;
                }

                // Take over computed controller PWM value
                current_reflow_oven_signals.pwm_controller_percent = ctrl.pwm_controller_percent;
                break;
        }

        // Write to serial port
        usb_packet_to_tiva.pwm_controller = 0.01f * current_reflow_oven_signals.pwm_controller_percent * 0xFFFF;
        usb_packet_to_tiva.status = 0;
        write(serial_port, &usb_packet_to_tiva, sizeof(usb_packet_to_tiva));

        // Allocate memory for read buffer, set size according to your needs
        uint8_t read_buf[256];

        // Set buffer to zero.
        memset(&read_buf, '\0', sizeof(read_buf));

        // Read bytes. The behaviour of read() (e.g. does it block?,
        // how long does it block for?) depends on the configuration
        // settings above, specifically VMIN and VTIME
        int num_bytes = read(serial_port, &read_buf, sizeof(read_buf));

        // n is the number of bytes read. n may be 0 if no bytes were received, and can also be -1 to signal an error.
        if (num_bytes < 0)
        {
            fprintf(stderr, "Error reading (error code %i)", errno);
            return 1;
        }

        // Check if we have read a Tiva-To-PC structure.
        if (num_bytes == sizeof(usb_serial_data_tiva_to_pc))
        {
            memcpy(&usb_packet_from_tiva, read_buf, num_bytes);
        }
        else
        {
            printf("Did NOT read a dedicated Tiva-to-PC packet\n");
        }

        // Print to terminal
        time_sec = 0.001f * timing.diff_ms;
        printf("------------------------------------------------------------------\n"
               "Time:                 % 8.3f s (of %i s)\n", time_sec, control_and_measurement_parameters.max_runtime_seconds);
        printf("Ambient temperature:   % 6.2f C\n", physical_bmp_data.temperature);
        // printf("Pressure:             % 8.2f Pa\n", physical_bmp_data.pressure);
        // printf("Thermocouple voltage: % 7.4f V\n", thermocouple_voltage);
        printf("Oven temperature:      %6.2f deg C", current_reflow_oven_signals.oven_temperature_deg_C);
        printf(" (thermocouple is %s)\n", current_reflow_oven_signals.thermocouple_is_open ? "open" : "closed");
        printf("Reference temperature: %6.2f deg C\n", ctrl.reference_deg_C);
        printf("PWM controller signal: %6.2f %%\n", current_reflow_oven_signals.pwm_controller_percent);

        // todo: think about whether a temperature condition (instead of a time condition)
        // would make sense for opening the door.
        if (time_sec > 550.0 + 60.0) {
            printf("\n\n#### Please open the door now! ############################################################\n\n\n");
        }

        // Log to file.
        if (control_and_measurement_parameters.sample_index >= 0 && !control_and_measurement_parameters.request_to_turn_off) {
            logSignalSample(&logging,
                            &control_and_measurement_parameters,
                            &timing,
                            &current_reflow_oven_signals,
                            &ctrl);
        }

        // Ready for next sample.
        control_and_measurement_parameters.sample_index += 1;

        if (timing.diff_ms >= 1000 * control_and_measurement_parameters.max_runtime_seconds) {
            break;
        }
    }

    //--------------------------------------------------
    if (!control_and_measurement_parameters.request_to_turn_off) {
        fclose(logging.log_fid);
    }
    close(serial_port);
    printf("* Closed the serial port and log file.\n");
    printf("* Finished cleanly -- bye.\n");
    return 0;
}

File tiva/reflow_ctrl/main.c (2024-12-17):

#include <stdbool.h>
#include <stdint.h>
#include "inc/hw_memmap.h"
#include "inc/hw_gpio.h"
#include "inc/hw_types.h"
#include "inc/hw_ssi.h"
#include "driverlib/sysctl.h"
#include "driverlib/gpio.h"
#include "driverlib/pin_map.h"
#include "driverlib/i2c.h"
#include "driverlib/adc.h"
#include "driverlib/ssi.h"

// USB from driverlib
#include "driverlib/usb.h"
#include "usblib/usblib.h"
#include "usblib/usbcdc.h"
#include "usblib/usb-ids.h"
#include "usblib/device/usbdevice.h"
#include "usblib/device/usbdcdc.h"
// Own USB files
#include "usb_serial_structs.h"
#include "../../host/usb_serial_data.h"

// For USB, also link the usblib and put the USB0DeviceIntHandler in the
// interrupt vector table (you do not need to define USB0DeviceIntHandler,
// it is likely defined in the usblib).
// If you fail to add USB0DeviceIntHandler to the ISR, you end up in the
// default interrupt.

//
// Definitions for the Bosch BMP280.
//
#define TEMPERATURE_SENSOR_PERIPHERAL_I2C_ADDRESS 0x76
#define TEMPERATURE_SENSOR_REGISTER_WHO_AM_I 0xD0
#define TEMPERATURE_SENSOR_TEMPERATURE_MSB 0xFA
#define TEMPERATURE_SENSOR_PRESSURE_MSB 0xF7
#define TEMPERATURE_SENSOR_REGISTER_CONTROL_REGISTER 0xF4
#define TEMPERATURE_SENSOR_REGISTER_CONFIG_REGISTER 0xF5


//*****************************************************************************
//
// Flags used to pass commands from interrupt context to the main loop.
//
//*****************************************************************************
#define COMMAND_PACKET_RECEIVED 0x00000001
#define COMMAND_STATUS_UPDATE   0x00000002

volatile uint32_t g_ui32Flags = 0;

// Global flag indicating that a USB configuration has been set.
static volatile bool g_bUSBConfigured = false;
// The USB data packet that we are receiving.
static volatile usb_serial_data_pc_to_tiva usb_packet_recv;
// The USB data packet that we are sending.
static volatile usb_serial_data_tiva_to_pc usb_packet_sent;

// 16-bit PWM value (0x0000 to 0xFFFF) for the controller
static volatile uint16_t ui16_PWM_Controller = 0;


//**********
// ADC
//**********
#define ADC_SEQUENCE_NUM    3 // was 0
#define ADC_SAMPLE_BUF_SIZE 1 // We're just using one sample


//*****************************************************************************
//
// Internal functions.
//
//*****************************************************************************
static void turnOnRedLed() {
    // Red: PF1
    uint8_t pin = GPIO_PIN_1;
    GPIOPinWrite(GPIO_PORTF_BASE, pin, pin);
}

static void turnOffRedLed() {
    uint8_t pin = GPIO_PIN_1;
    GPIOPinWrite(GPIO_PORTF_BASE, pin, 0);
}

static void turnOnGreenLed() {
    // Green: PF3
    uint8_t pin = GPIO_PIN_3;
    GPIOPinWrite(GPIO_PORTF_BASE, pin, pin);
}

static void turnOffGreenLed() {
    uint8_t pin = GPIO_PIN_3;
    GPIOPinWrite(GPIO_PORTF_BASE, pin, 0);
}

static void turnOnBlueLed() {
    // Blue: PF2
    uint8_t pin = GPIO_PIN_2;
    GPIOPinWrite(GPIO_PORTF_BASE, pin, pin);
}

static void turnOffBlueLed() {
    uint8_t pin = GPIO_PIN_2;
    GPIOPinWrite(GPIO_PORTF_BASE, pin, 0);
}

int writeIMURegister(const uint8_t ui8_register, const uint8_t ui8_value) {

    //
    // See https://forum.digikey.com/t/i2c-communication-with-the-ti-tiva-tm4c123gxl/13451
    //

    // Set the third argument to false, as we want to write to the peripheral.
    // The third argument is the read/not write flag.
    // read/not write = false <==> not read/write = true
    I2CMasterSlaveAddrSet(I2C1_BASE, TEMPERATURE_SENSOR_PERIPHERAL_I2C_ADDRESS, false);

    I2CMasterDataPut(I2C1_BASE, ui8_register);
    I2CMasterControl(I2C1_BASE, I2C_MASTER_CMD_BURST_SEND_START);
    while (I2CMasterBusy(I2C1_BASE)) { } // note: not BusBusy, but Busy

    I2CMasterDataPut(I2C1_BASE, ui8_value);
    I2CMasterControl(I2C1_BASE, I2C_MASTER_CMD_BURST_SEND_FINISH);
    while (I2CMasterBusy(I2C1_BASE)) { } // note: not BusBusy, but Busy

    return 0;
}

int readIMURegister(const uint8_t ui8_register, uint8_t *ui8_value) {

    uint32_t ui32_received = 0;

    // Set to false as we want to write to the peripheral.
    I2CMasterSlaveAddrSet(I2C1_BASE, TEMPERATURE_SENSOR_PERIPHERAL_I2C_ADDRESS, false);
    I2CMasterDataPut(I2C1_BASE, ui8_register);
    I2CMasterControl(I2C1_BASE, I2C_MASTER_CMD_SINGLE_SEND);

    // Note: You need to either use "I2CMasterBusy" (without the word "Bus")
    // _or_ use "I2CMasterBusBusy" in conjunction with waiting via "SysCtlDelay".
    // Using "I2CMasterBusBusy" does not work --> you would end up performing
    // a reading operation only (without telling the peripheral which register
    // to read in the first place).
    while(I2CMasterBusy(I2C1_BASE)) {}

    // Now read the value.
    I2CMasterSlaveAddrSet(I2C1_BASE, TEMPERATURE_SENSOR_PERIPHERAL_I2C_ADDRESS, true);
    I2CMasterControl(I2C1_BASE, I2C_MASTER_CMD_SINGLE_RECEIVE);

    // Note that we need to wait here for the uC to actually receive
    // the data via the I2C bus before calling "I2CMasterDataGet".
    while(I2CMasterBusy(I2C1_BASE)) {}

    ui32_received = I2CMasterDataGet(I2C1_BASE);

    // Note that we read from the bus in any case.
    // We just do not return the value if it is not wanted.
    if (!ui8_value) {
        return -1;
    }

    *ui8_value = (uint8_t) (0x000000FF & ui32_received);

    return 0;
}
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

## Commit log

2024-01-28 Added a first version of the reflow controller
    [controller-B_Cu.gbr, controller-B_Mask.gbr, controller-B_Paste.gbr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]
2024-02-10 Added first box to hold the reflow controller PCB
    [create_box.scad]
2024-02-10 Made box a bit faster to print
    [create_box.scad]
2024-02-10 Added dimensions to board layout
    [controller.kicad_pcb]
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2024-03-03 Added required changes for the printed box
    [create_box.scad]
2024-03-03 Incorporated changes to the reflow controller schematic (v1.0.0 to v1.0.1)
    Also incorporated some changes to the board, but did not place
    and route the two additional resistors.
    [controller.kicad_pcb, controller.kicad_sch]
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2024-03-30 Added USB on the Tiva
    Added USB code, includes, library, and interrupt handler.
2024-03-30 Updated signals from tiva to host to carry
    The struct that carries the signals from the
    tiva to the host now contains the temperature
    and pressure measurement values as well as
    the trimming values.
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2024-03-30 Read trimming values and evaluate physical temperature and pressure
    Include code from the sensor API in order to compute
    the physical values of the temperature and pressure.
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2024-03-30 Added schematic for thermocouple amplifier
    [controller.kicad_sch, thermoamp.kicad_sch]
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2024-03-30 Updated schematic for thermo couple amp
    [thermoamp.kicad_sch]
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2024-03-30 Updated schematic
    [thermoamp.kicad_sch]
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2024-03-30 Changed voltage divider values to ensure 3.3V limit on Tiva
    [thermoamp.kicad_sch]
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2024-03-31 Log physical values and plot them in Python
    Replaced logging of the MSB and LSB by
    loggin of the physical values (as float or double).
    Created a script to read and plot the traces
    in Python.
    [host_main.c]
2024-04-01 Added analog thermo couple schematic and board
    [thermo-sensor-analog.kicad_pcb, thermo-sensor-analog.kicad_sch]
2024-04-03 Added digital thermo couple schematic and board
    [thermo-sensor-digital.kicad_pcb, thermo-sensor-digital.kicad_sch]
2024-04-03 Prepared thermo sensor boards for fabrication
    This is the version with which I created the gerber files.
    [thermo-sensor-analog.kicad_pcb]
2024-05-22 Small refactoring
    [create_box.scad]
2024-05-22 Updated comments
    [create_box.scad]
2024-05-22 Added thermo amplifier pattern
    [create_box.scad]
2024-05-22 Added 20 mm more space for wires
    [create_box.scad]
2024-05-22 Increased height
    [create_box.scad]
2024-05-22 Added holes for mounting a cover
    [create_box.scad]
2024-05-23 Added holes to mount thermo couple banana plugs
    [create_box.scad]
2024-05-24 Added mount for rail
    [create_box.scad]
2024-05-24 First attempt at reducing material
    [create_box.scad]
2024-05-25 Added dedicated structures to connect the mounting hole pattern
    [create_box.scad]
2024-05-25 Adjusted mounting holes for rail to fit M4
    [create_box.scad]
2024-05-26 Created lid for box
    [create_box.scad, create_lid.scad, lid_part.scad]
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2024-08-03 Fixed compile errors on Raspberry Pi
    [bmp.h]
2024-08-03 Fixed end time abort condition
    [host_main.c]
2024-08-03 Explicitly set the GPIO PF4 as 8 mA output
    That did not help against the issues with
    the PWM not working correctly though
    [main.c]
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2024-08-03 Fixed automatic OS identification on the RPi
    [host_main.c]
2024-08-03 Fit model to 100 percent PWM with stop after 100 deg C have been reached
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2024-08-19 Started work on PCB mount
    [create_pcb_mount.scad, parameters.scad]
2024-08-19 Added screw mounting holes
    [create_pcb_mount.scad]
2024-08-19 Renamed height variable
    [create_pcb_mount.scad]
2024-08-19 Introduced variables for length and width of the mount
    [create_pcb_mount.scad]
2024-08-19 Improved parameterization
    [create_pcb_mount.scad]
2024-08-19 Created first version of the PCB mount
    [create_pcb_mount.scad]
2024-08-19 Added stencil mount
    [create_pcb_mount.scad, create_stencil_mount.scad, parameters.scad]
2024-08-19 Created PCB and stencil STLs for checking the assembly
    [create_pcb.scad, create_stencil.scad]
2024-08-19 Created the overall mount assembly view
    [create_assembly.scad]
2024-08-19 Adjusted dimensions
    [create_assembly.scad, parameters.scad]
2024-08-19 Added plate
    [create_assembly.scad, create_plate.scad]
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2024-10-06 Added Tiva and impedance converter board
    [tiva-board.kicad_pcb, tiva-board.kicad_sch]
2024-10-06 Created Gerber files for Tiva board
    [tiva-board.kicad_pcb]
2024-10-06 Extended documentation on Tiva board
    [tiva-board.kicad_pcb]
2024-10-19 Added mounting hole distance dimensions to PCB layout
    [tiva-board.kicad_pcb]
2024-10-19 Created separate 3D part for the Tiva board
    [create_tiva_box_addon.scad]
2024-10-19 Updated todos for the box
    [create_box.scad]
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2024-11-10 Fixed percent sign escaping
    [host_main.c]
2024-11-10 Replaced individual variables by control parameter struct
    [host_main.c]
2024-11-10 Partially replaced usage of controller struct by reflow oven signals struct
    [host_main.c]
2024-11-10 Initialize sample index with -1 to ensure a valid first measurement in the log file
2024-11-10 Fix: inserted space
2024-11-10 Implemented functionality to turn off oven directly (also disabled signal logging in that case)
2024-11-10 Reworked logging: added thermocouple open indicator, cleaned-up terminal printing
    [host_main.c]
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2024-11-10 Replaced PI by PID controller; Tuned controller on profile
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2024-11-10 Initialized and reworked controller parameter struct
    [host_main.c]
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2024-11-10 Added test profile for quick tests with short runtime and (almost) no heating up
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2024-11-10 Performed first soldering task (wheel speed sensor); Adapted todos; Wrote short report
2024-12-17 Updated resistor values on the Tiva board
    [tiva-board.kicad_pcb, tiva-board.kicad_sch]
2024-12-17 Added BMP280 mount
    [create_bmp280_addon.scad]
2024-12-17 Reworked BMP280 mount based on the first print
    [create_bmp280_addon.scad]
2024-12-17 Added comments about screw sizes
    [create_box.scad]
2024-12-17 Rearranged points and removed one point
    [create_tiva_box_addon.scad]
2024-12-17 Added DIN rail connector to Tiva board mount
    [create_tiva_box_addon.scad]
2024-12-17 Import the BMP280 mount into the Tiva board mount
    [create_tiva_box_addon.scad]
2024-12-17 Fixed date of first soldering in solder report
2024-12-17 Reduced CS low time
    Reduced the time that the GPIO output which is used as
    the chip select (CS) signal is low.
    The low time was very long, perhaps contributing
    to the bit errors (bit shifting errors)
    on the SPI data line.
    [main.c]
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2024-12-17 Use push-pull instead of weak pull-up on CS
    Instead of the weak pull-up, use push-pull on the GPIO
    that is used for chip select.
    This did not solve the problem of the CS line
    going to 1 Volt sometimes though.
    [main.c]
2024-12-17 Introduced waiting and toggling on CS
    Wait some time after the data on the SPI has been transferred.
    Also, toggle the chip select GPIO after the transmission
    (did not improve the bit shift errors).
    Also toggle it before.
    It seems that this did the trick and avoids the
    1 Volt state which in turn led to bit shift errors.
    [main.c]
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2024-12-23 Added measurement of second soldered PCB
    This is the Cortex M4 board that I soldered on Dec 23, 2024.
    When opening the door to the oven, the thermocouple
    was open, so the temperature measurements are not correct.
    It was slightly raining on that day.
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
